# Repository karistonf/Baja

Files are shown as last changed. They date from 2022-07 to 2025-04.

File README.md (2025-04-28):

# Baja

## Projeto Baja SAE UEM - Equipe Capibaja
O Projeto Capibaja é um projeto acadêmico que visa a construção de um carro off-road monoposto movido a gasolina. A parte elétrica do veículo é responsável pela coleta de dados do carro e pela interface com o piloto, incluindo o monitoramento de velocidade e rodagem, bem como a saúde dos demais componentes do veículo. Não cabe a elétrica a fabricação de injeção eletrônica.

# Capacidades e objetivos do projeto
## Coleta de dados
* Velocidade (individual por roda) 
* Rodagem
* Temperatura CVT e motor
* Coordenadas de GPS
* Nível de Combustível
* Tensão da bateria
* Pressão nos freios
* E o mais importante, uma fita de led estilosa

# Construção

No projeto Capibaja, adotamos uma abordagem descentralizada para a coleta de dados, utilizando várias pequenas placas denominadas "placas gerais" (você pode obter mais informações sobre elas nos diretórios deste commit). Cada sensor é conectado a um microcontrolador, que por sua vez possui acesso à rede CAN de todo o veículo. Essas placas gerais são específicas para cada sensor e têm a função de ler os dados do sensor e transmitir seu valor na rede CAN.

Além das placas gerais, haverá uma segunda placa PCB, chamamos ela de placa principal, acessível ao piloto. Essa placa contará com uma tela e botões, servindo como interface para exibir os dados do carro em tempo real.

# Placa geral
Por enquanto é um esboço
Essa será a placa que coletara os dados dos sensores

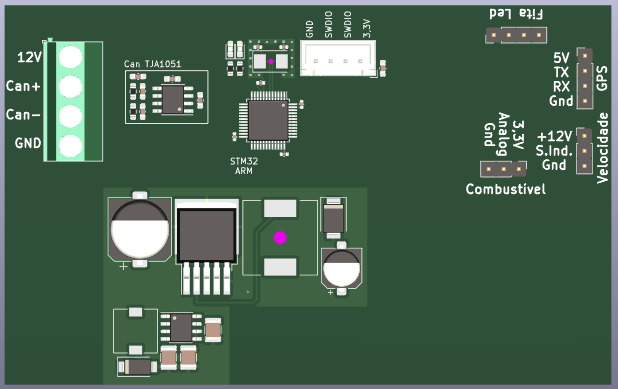
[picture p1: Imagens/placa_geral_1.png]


# Placa principal
Essa será a placa que mostrará ao piloto as informações necessárias
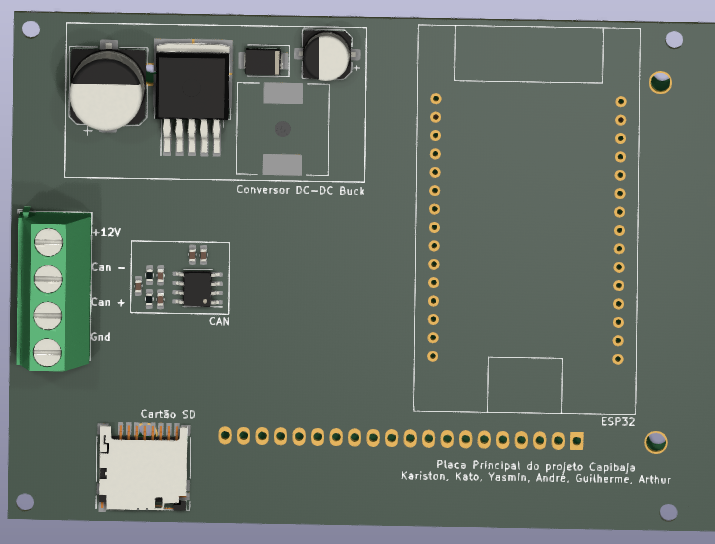
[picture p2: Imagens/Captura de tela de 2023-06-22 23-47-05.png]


# À fazer
* Corrigir footprint SD Card, Display 128x64
* Colocar os botões no lado correto

# Adicionar

# Feito
* Can transmissor

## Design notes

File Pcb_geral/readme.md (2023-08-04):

# Descrição da placa geral

## A placa geral será responsável por coletar estes dados:

Relacionando os sensores usados com o protocolo para leitura do sensor

* Velocidade -> Sensor Indutivo -> porta digital
* Sensor de combustível -> Sensor reed switch (desenvolvido pela nossa equipe) -> porta analógica
* Célula de carga -> Analógica
* Sensor de temperatura motor -> Analógica
* Acelerômetro e giroscópio -> I2C
* Sensor de temperatura CVT -> I2C
* GPS -> Serial
* Sensor de pressão do fluido de freio -> * falta escolher o sensor para definir *
* Radio Frequência -> SPI 

## O que foi feito

3/ago

* Foi implementado proteção contra excesso de corrente e tensão contrária.
* Adicionado os conectores para os sensores e dispositivos externos, posicionados, e serigrafia indicando corretamente as conexões.
* Foi arrumado a posição dos componentes do can
* Inseriu-se um conector tipo borne para conectar ao chicote do veículo

## Coisas à fazer

3/ago

* Colocar optoacoplador
* Exemplo de comunicação para GPS, e quais pinos conectar
* Confirmar pinos para comunicação I2C
* Exemplo e confirmar pinos para conectar a fita de led
* Usar fita de led 12V
* Verificar se a ligação do mosfet
* reduzir o tamanho do regulador de tensão de 5V (se dimensionado o consumo de corrente)
* desenhar o contorno da placa, e caixa para proteção

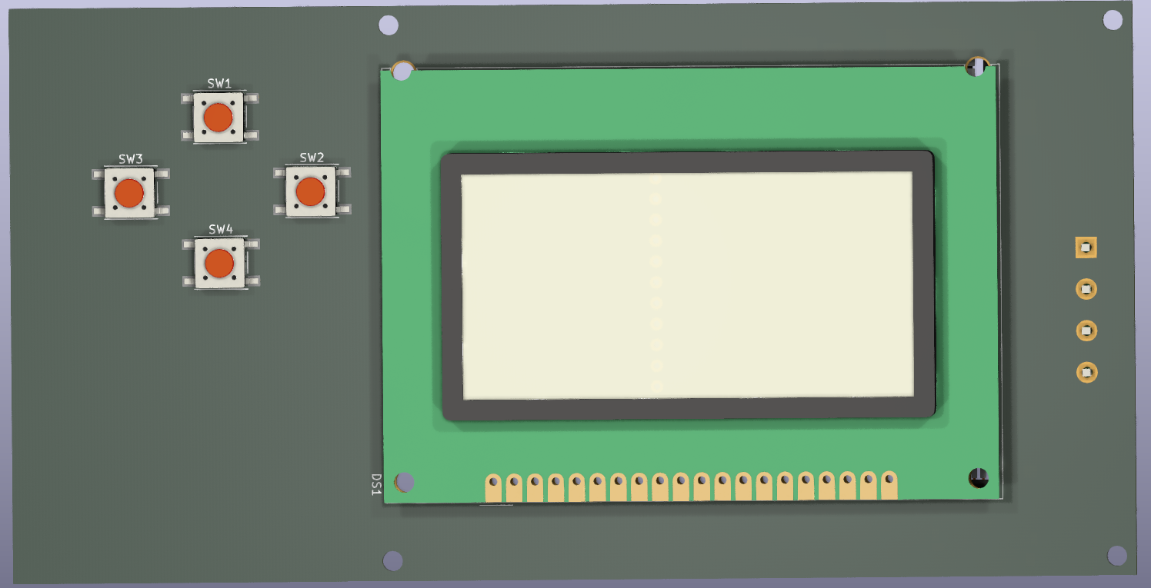
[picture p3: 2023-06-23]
Imagens/Captura de tela de 2023-06-22 23-47-43.png

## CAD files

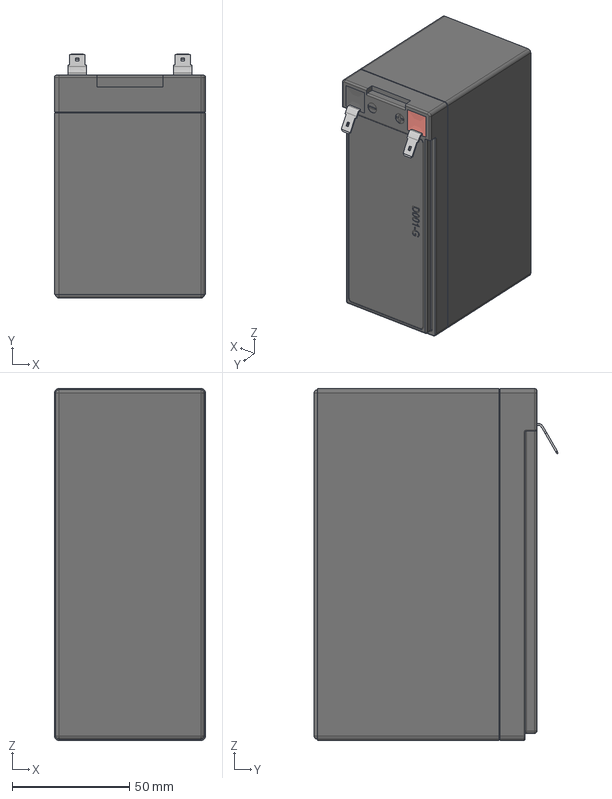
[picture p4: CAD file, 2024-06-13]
Batería 12V-7Ah 150mm x 65mm x 100mm v5.step
64.5 x 104.0 x 150.0 mm

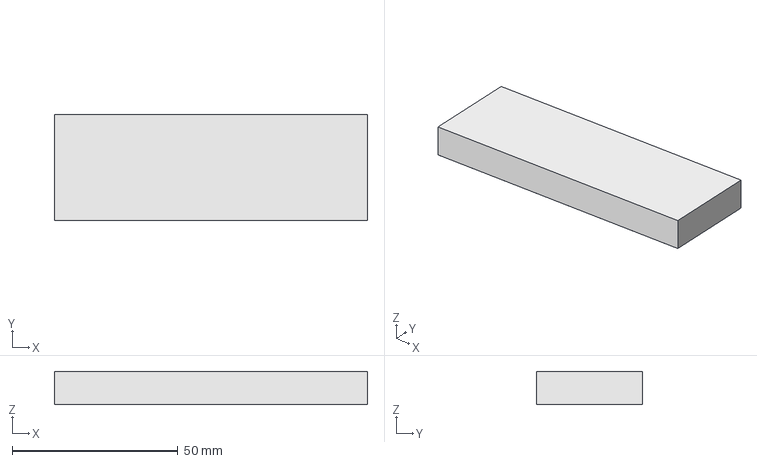
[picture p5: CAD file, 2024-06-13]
Desenhos 3D/bateria.FCStd
94.3 x 31.8 x 10.0 mm
ShapeBinder

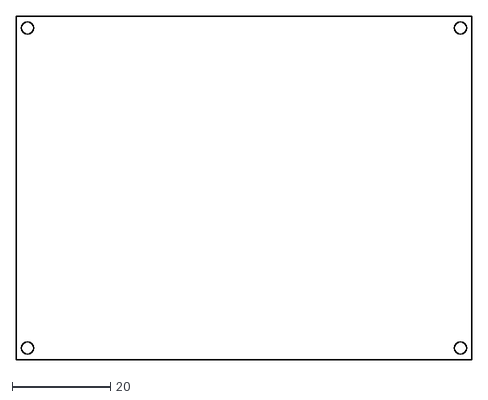
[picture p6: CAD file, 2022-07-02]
PCB/Formato Placa/Formato_da_placa-Sketch.dxf
93.0 x 70.0

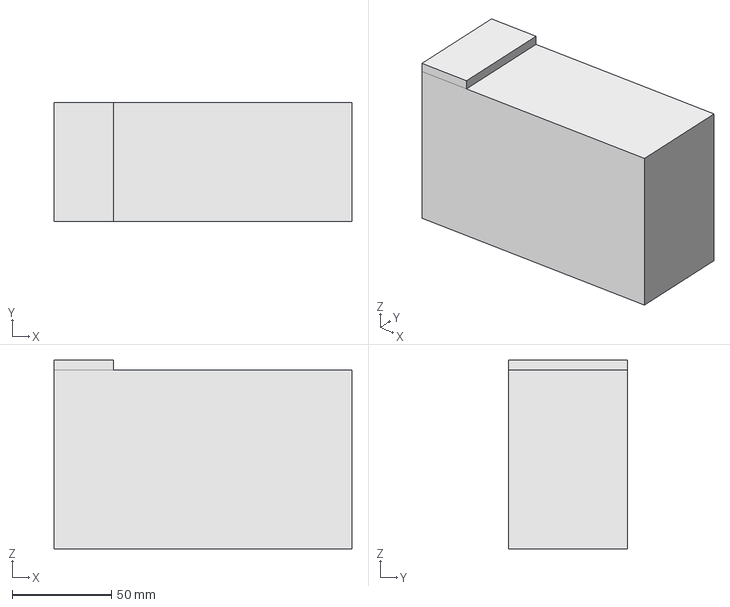
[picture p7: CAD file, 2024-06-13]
Desenhos 3D/Suporte_bateria.FCStd
150.0 x 60.0 x 95.0 mm

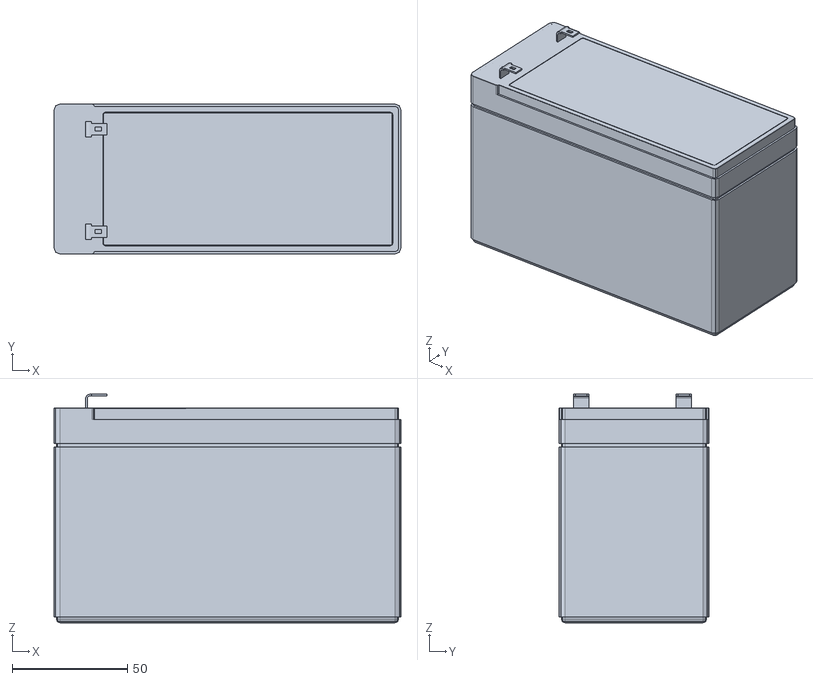
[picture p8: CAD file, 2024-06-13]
Desenhos 3D/Batterie.stl
150.5 x 65.0 x 99.1

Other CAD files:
PCB/Formato Placa/Formato_da_placa.FCStd

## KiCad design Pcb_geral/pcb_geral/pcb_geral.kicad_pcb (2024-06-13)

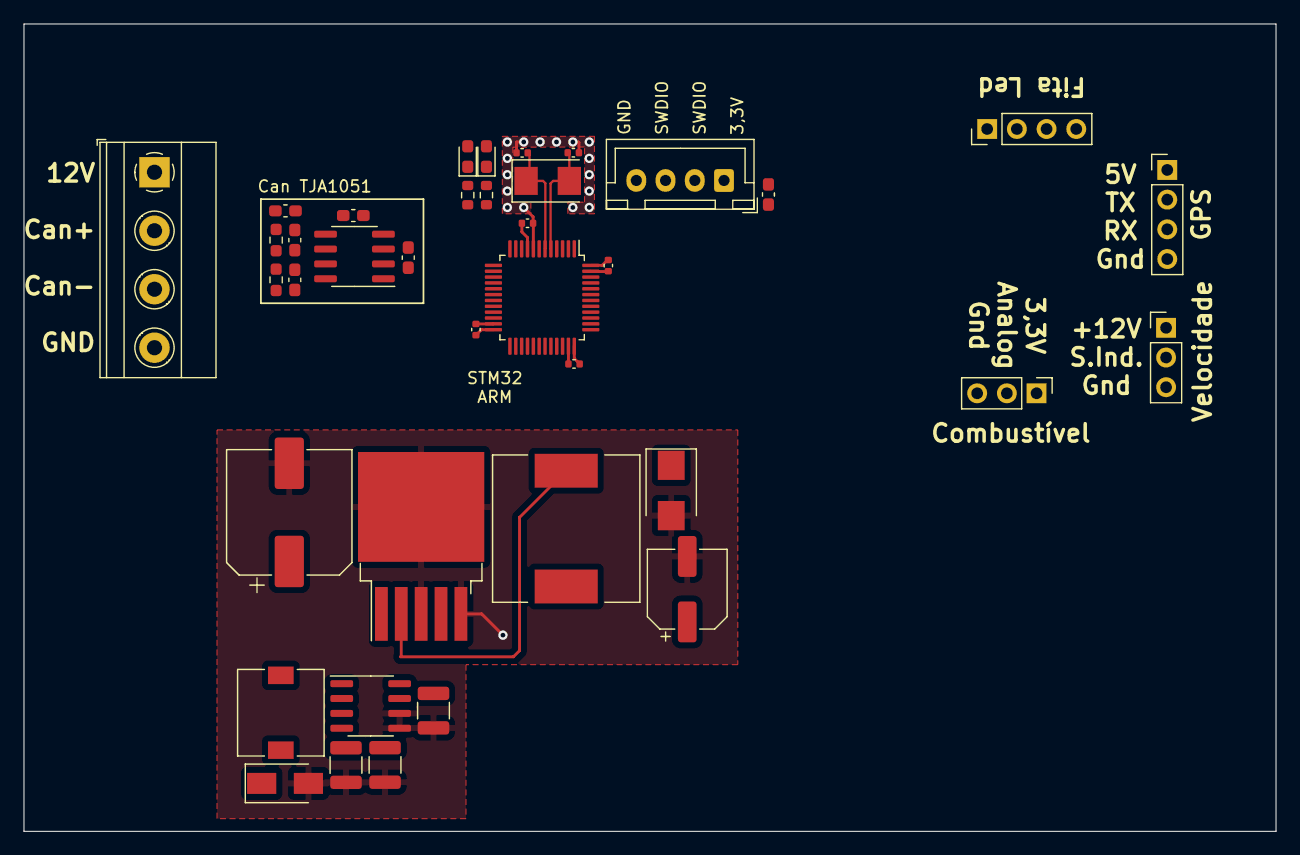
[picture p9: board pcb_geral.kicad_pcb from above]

Board: 2 copper layers, 107.1 x 69.0 mm, 38 parts (0 on the bottom side), 14 nets.

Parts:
C1: 10uF; C_1210_3225Metric
C2: 680uF; CP_Elec_10x10.5
C3, C5: 100uF; C_1210_3225Metric
C4: 220uF; CP_Elec_6.3x5.4
C6: 100nF; C_0603_1608Metric_Pad1.08x0.95mm_HandSolder
C7: 47nF; C_0603_1608Metric_Pad1.08x0.95mm_HandSolder
C8: 100µF; C_0603_1608Metric_Pad1.08x0.95mm_HandSolder
C9, C10, C11, C12: 100µF; C_0402_1005Metric
C13, C14: 100pF; C_0603_1608Metric_Pad1.08x0.95mm_HandSolder
C15: 4,7uF; C_0603_1608Metric_Pad1.08x0.95mm_HandSolder
CC1, CC2: 33pF; C_0402_1005Metric
D1: D; D_SMA
D2: 1N5824; D_SMB
D3, D4: LED; LED_0603_1608Metric_Pad1.05x0.95mm_HandSolder
J1: Conn_01x04_Female; TerminalBlock_Phoenix_MKDS-1,5-4_1x04_P5.00mm_Horizontal
J2, J3: Conn_01x03_Female; PinHeader_1x03_P2.54mm_Vertical
J5, J6: Conn_01x04_Female; PinHeader_1x04_P2.54mm_Vertical
L1: 100uH; L_7.3x7.3_H4.5
L2: 33uH; L_12x12mm_H8mm
Prog1: Conn_01x04_Female; JST_XH_B4B-XH-A_1x04_P2.50mm_Vertical
R1, R2: 510; R_0603_1608Metric
R3, R4: 60; R_0603_1608Metric_Pad0.98x0.95mm_HandSolder
U1: LM2594M-3.3; SOIC-8_3.9x4.9mm_P1.27mm
U2: LM2596S-5; TO-263-5_TabPin3
U3: STM32F103C6Tx; LQFP-48_7x7mm_P0.5mm
U4: TJA1051T-3; SOIC-8_3.9x4.9mm_P1.27mm
Y2: 8Mhz; Crystal_SMD_5032-2Pin_5.0x3.2mm

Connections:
+3V3: C3.1, C5.1, C6.1, C8.1, C9.1, C10.1, C11.1, C12.1, D3.2 (A), D4.2 (A), L1.2, Prog1.1, U1.4 (FB), U3.9 (VDDA), U3.24 (VDD), U3.36 (VDD), U3.48 (VDD), U4.5 (VIO)
+5V: C4.1, C6.2, C7.1, J5.1, L2.2, U2.4 (FB), U4.3 (VCC)
+12V: C1.1, C2.1, J2.1, U1.7 (VIN), U2.1 (VIN)
/Can+: C13.2, J1.3, R3.1, U4.7 (CANH)
/Can-: C14.2, J1.2, R4.1, U4.6 (CANL)
/OSC+: CC2.1, U3.6 (PD1), Y2.1
/OSC-: CC1.1, U3.5 (PD0), Y2.2
/Out_pwr_indutor: D2.1 (K), L2.1, U2.2 (OUT)
GND: C1.2, C2.2, C3.2, C4.2, C5.2, C7.2, C8.2, C9.2, C10.2, C11.2, C12.2, C13.1, C14.1, C15.1, CC1.2, CC2.2, D1.2 (A), D2.2 (A), J1.4, J2.3, J5.4, Prog1.4, R2.2, U1.5 (~ON/OFF), U1.6 (GND), U2.3 (GND), U2.5 (~ON/OFF), U3.8 (VSSA), U3.23 (VSS), U3.35 (VSS), U3.47 (VSS), U4.2 (GND)
unnamed: C15.2, R3.2, R4.2
unnamed: D1.1 (K), L1.1, U1.8 (OUT)
unnamed: D3.1 (K), R1.2
unnamed: D4.1 (K), R2.1
PC13: R1.1, U3.2 (PC13)

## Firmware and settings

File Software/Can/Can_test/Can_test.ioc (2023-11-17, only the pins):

Mcu.UserName=STM32F103C8Tx
PA11.Signal=CAN_RX
PA12.Signal=CAN_TX
PA13.Signal=SYS_JTMS-SWDIO
PA14.Signal=SYS_JTCK-SWCLK
PA4.Signal=GPIO_Output
PC13-TAMPER-RTC.Signal=GPXTI13
PC14-OSC32_IN.Signal=RCC_OSC32_IN
PC15-OSC32_OUT.Signal=RCC_OSC32_OUT
PD0-OSC_IN.Signal=RCC_OSC_IN
PD1-OSC_OUT.Signal=RCC_OSC_OUT

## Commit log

2022-07-02 commit inicial, com primeiras atualizaçoes da pcb do baja 2023
    [Formato_da_placa-Sketch.dxf, Formato_da_placa.FCStd, Tela.csv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]
2023-02-23 commit inicial da placa de uso geral do baja
    [pcb_geral.kicad_pcb, pcb_geral.kicad_sch]
2023-04-27 cristal clock posicionado, seguindo as boas praticas de desenho de PCI
    [pcb_geral.kicad_pcb, pcb_geral.kicad_sch]
2023-04-27 plano de alimentação, saparar dos planos alimentação do plano digital
    [pcb_geral.kicad_pcb, pcb_geral.kicad_sch]
2023-06-23 foi adicionado o TJA1051 de can na placa. Falta os footprints e as conexão no microcontrolador
    [pcb_geral.kicad_pcb]
2023-06-23 adição dos footprint do modulo de can, adição dos botoes, e desenho de areas no silkscreen
    [Tela.kicad_pcb, Tela.kicad_sch]
2023-06-23 placa geral, add can e footprints
    [pcb_geral.kicad_pcb, pcb_geral.kicad_sch]
2023-08-04 atualizacoes na placa geral, posicionamento do can, adição dos pontos para conexão para sensores e dispositivos externos, sistemas de proteção contra corrente excessiva e reversão de tensão, silk mai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
    [pcb_geral.kicad_pcb, pcb_geral.kicad_sch]
2023-11-17 prog can
    [arm.cfg]
2024-06-13 add 3d
    [Batería 12V-7Ah 150mm x 65mm x 100mm v5.step, Batterie.stl, Suporte_bateria.FCStd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]
